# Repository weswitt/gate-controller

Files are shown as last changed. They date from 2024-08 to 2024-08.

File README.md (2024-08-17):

This project is a PCB design for controlling a Liftmaster gate operator from Home Assistant. 

The PCB design was done in KiCad 8.0, which is an open source electronic design tool. This project includes all of the KiCad project files so that you can modify the PCB if needed. I've also included a GERBER.ZIP file that can be used to simply have the PCB printed by someplace like JLPCB.

This project includes a bill of materials with URLs for all the parts necessary to build the board. I've sourced the part from DigiKey and Amazon.

The integration of the gate controller into Home Assistant is accomplished using ESPHome. This project includes the YAML file necessary to build and flash the firmware into the gate controller. You'll need to edit the YAML file and change the lines specified to customize to your environment.

This project includes datasheets for every component used on the gate controller board.

The gate controller board uses an ESP32-WROOM-32U microcontroller. This variant of the ESP32 uses an external antenna to improve the Wifi connectivity.

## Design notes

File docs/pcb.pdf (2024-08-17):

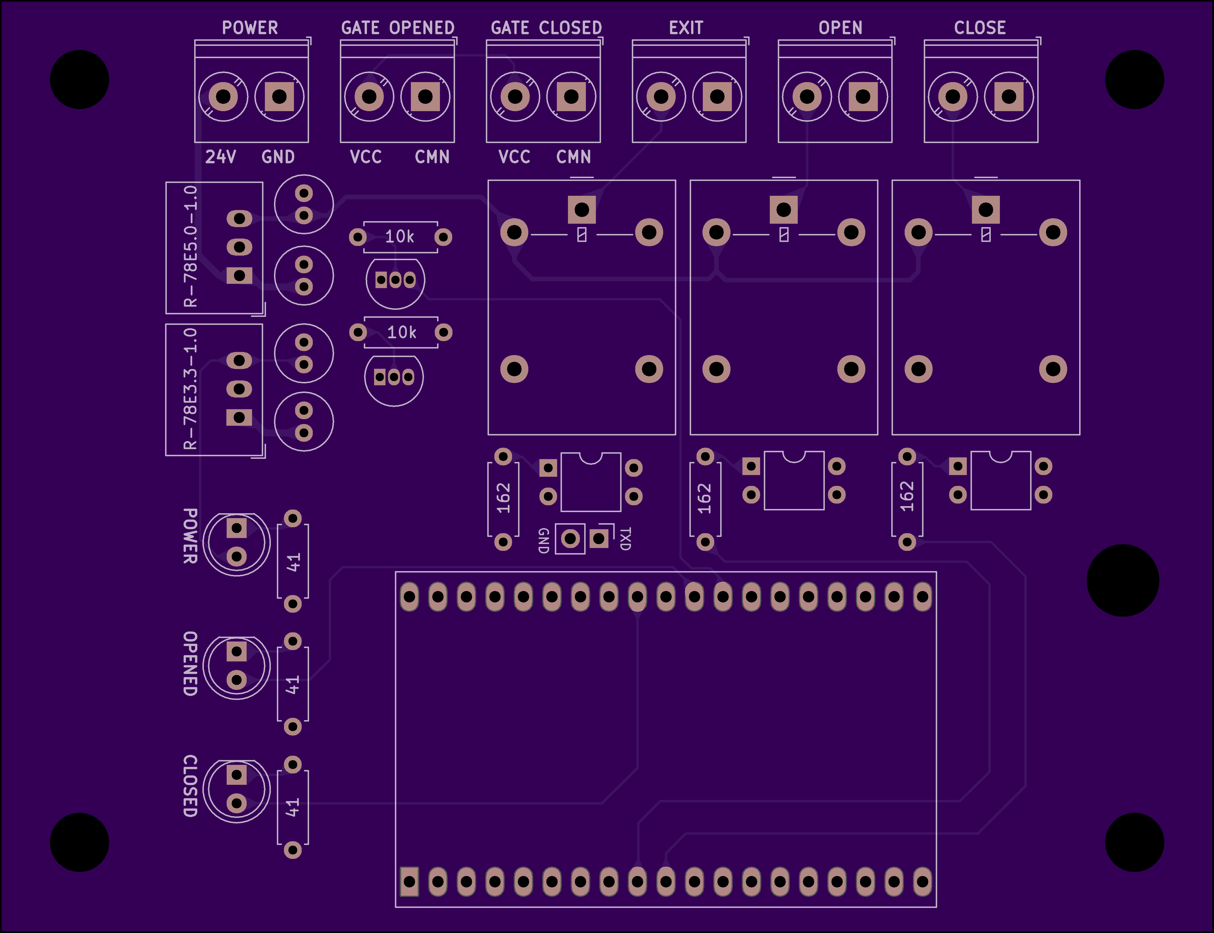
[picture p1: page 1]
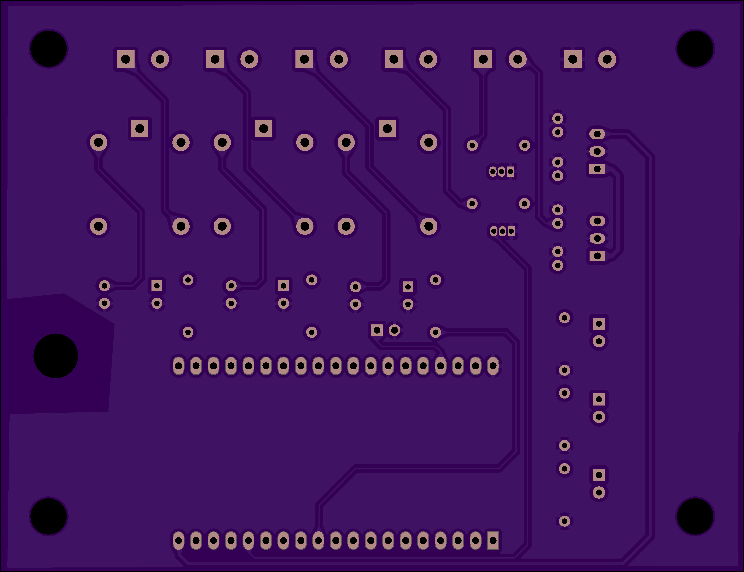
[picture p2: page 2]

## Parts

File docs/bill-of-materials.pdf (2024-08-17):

Item | Qty | Price | Extended | URL
relay | 3 | $1.62 | $4.86 | https://www.digikey.com/en/products/detail/omron-electronics-inc-emc-div/G5LE-1A4-DC5/369019
2n2222 | 2 | $0.40 | $0.80 | https://www.digikey.com/en/products/detail/onsemi/PN2222ABU/6534
fod852 | 3 | $1.08 | $3.24 | https://www.digikey.com/en/products/detail/onsemi/FOD852/1054017
terminal | 6 | $0.50 | $3.00 | https://www.digikey.com/en/products/detail/phoenix-contact/1935161/568614
capacitor | 4 | $0.38 | $1.52 | https://www.digikey.com/en/products/detail/nichicon/UPW1V100MDD/589590
red led | 1 | $0.36 | $0.36 | https://www.digikey.com/en/products/detail/liteon/LTL2R3KEK/573572
green led | 1 | $0.38 | $0.38 | https://www.digikey.com/en/products/detail/liteon/LTL2P3KGKNN/573567
yellow led | 1 | $0.40 | $0.40 | https://www.digikey.com/en/products/detail/liteon/LTL2R3KSK/573576
3v3 converter | 1 | $3.92 | $3.92 | https://www.digikey.com/en/products/detail/recom-power/r-78e3-3-1-0/5327711
5v converter | 1 | $3.92 | $3.92 | https://www.digikey.com/en/products/detail/recom-power/R-78E5-0-1-0/4930585
162 resistor | 3 | $0.10 | $0.30 | https://www.digikey.com/en/products/detail/yageo/MFR-25FBF52-162R/12837
41 resistor | 3 | $0.10 | $0.30 | https://www.digikey.com/en/products/detail/yageo/MFR-25FBF52-41R2/12720
10k resistor | 2 | $0.10 | $0.20 | https://www.digikey.com/en/products/detail/yageo/MFR-25FBF52-10K/13219
esp32u | 1 | $9.99 | $9.99 | https://www.amazon.com/dp/B09BM1QW29
antennea | 1 | $8.59 | $8.59 | https://www.amazon.com/dp/B01KBU61S8

$41.78

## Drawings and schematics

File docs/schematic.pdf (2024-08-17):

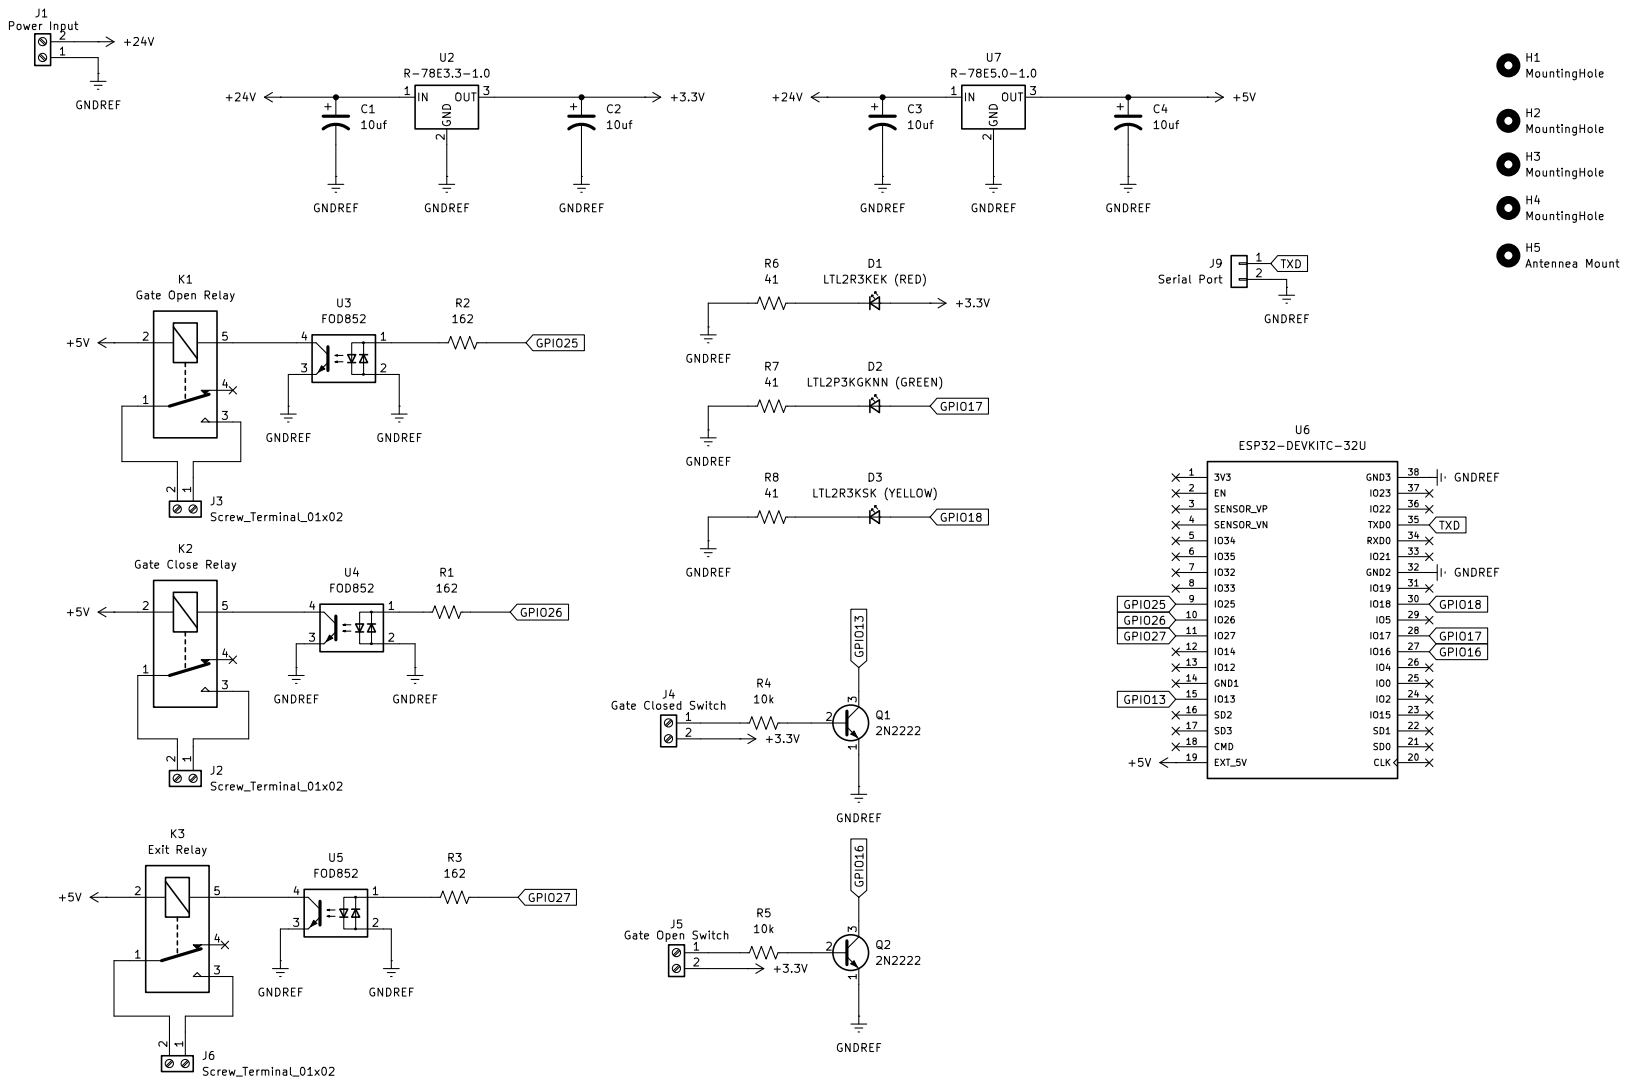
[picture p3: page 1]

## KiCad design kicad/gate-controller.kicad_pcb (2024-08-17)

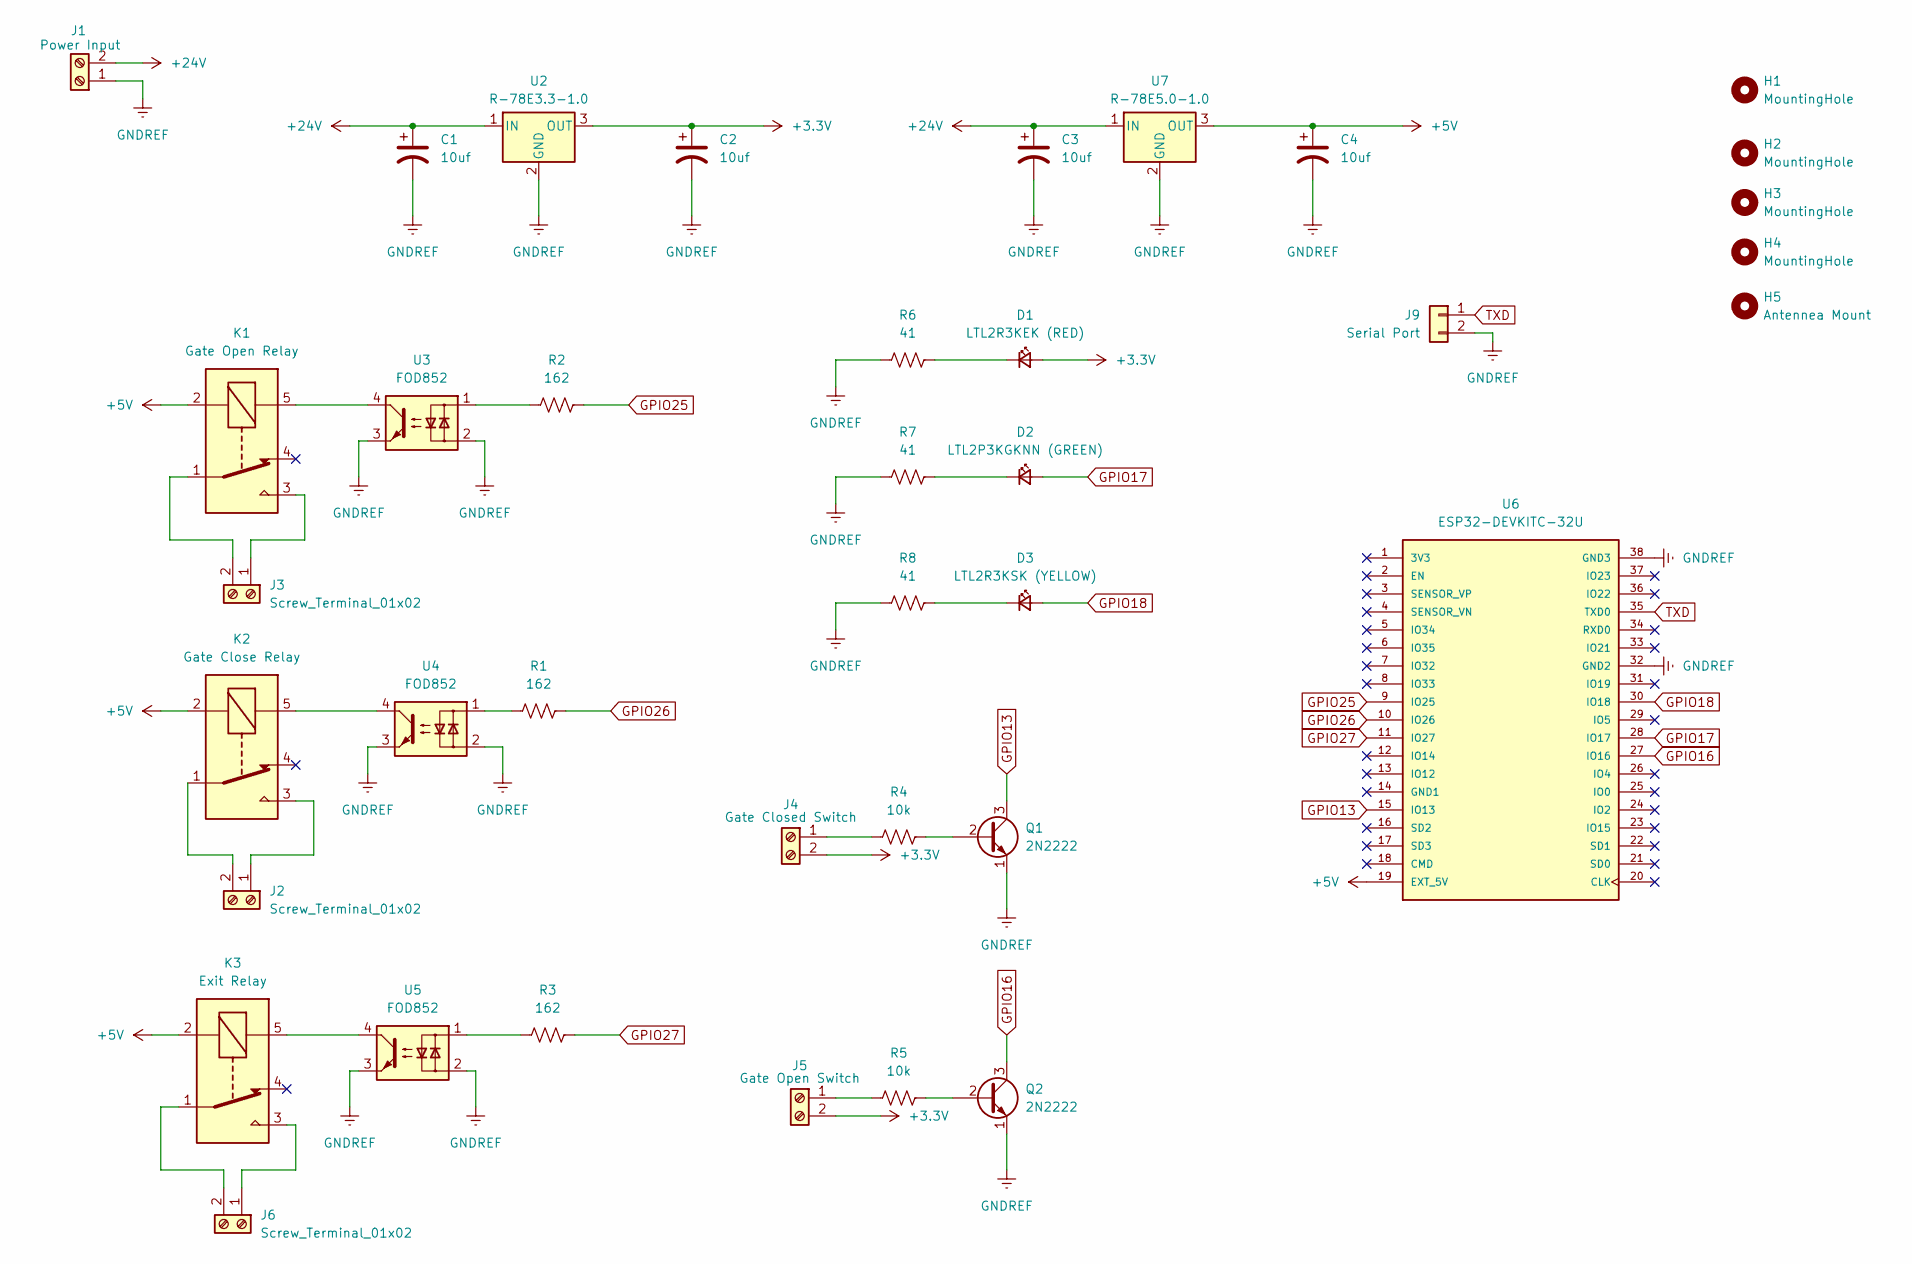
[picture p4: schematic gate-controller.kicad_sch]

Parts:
C1, C2, C3, C4: 10uf; C_Radial_D5.0mm_H11.0mm_P2.00mm
D1: LTL2R3KEK (RED); LED_D5.0mm_Clear
D2: LTL2P3KGKNN (GREEN); LED_D5.0mm_Clear
D3: LTL2R3KSK (YELLOW); LED_D5.0mm_Clear
H1, H2, H3, H4: MountingHole; MountingHole_5.3mm_M5
H5: Antennea Mount; MountingHole_6.5mm
J1: Power Input; TerminalBlock_Phoenix_PT-1,5-2-5.0-H_1x02_P5.00mm_Horizontal
J2, J3, J6: Screw_Terminal_01x02; TerminalBlock_Phoenix_PT-1,5-2-5.0-H_1x02_P5.00mm_Horizontal
J4: Gate Closed Switch; TerminalBlock_Phoenix_PT-1,5-2-5.0-H_1x02_P5.00mm_Horizontal
J5: Gate Open Switch; TerminalBlock_Phoenix_PT-1,5-2-5.0-H_1x02_P5.00mm_Horizontal
J9: Serial Port; PinHeader_1x02_P2.54mm_Vertical
K1: Gate Open Relay; Relay_SPDT_Omron-G5LE-1
K2: Gate Close Relay; Relay_SPDT_Omron-G5LE-1
K3: Exit Relay; Relay_SPDT_Omron-G5LE-1
Q1, Q2: 2N2222; TO-92_Reverse
R1, R2, R3: 162; R_Axial_DIN0207_L6.3mm_D2.5mm_P7.62mm_Horizontal
R4, R5: 10k; R_Axial_DIN0207_L6.3mm_D2.5mm_P7.62mm_Horizontal
R6, R7, R8: 41; R_Axial_DIN0207_L6.3mm_D2.5mm_P7.62mm_Horizontal
U2: R-78E3.3-1.0; Converter_DCDC_RECOM_R-78E-0.5_THT
U3, U4, U5: FOD852; DIP-4_W7.62mm
U6: ESP32-DEVKITC-32U
U7: R-78E5.0-1.0; Converter_DCDC_RECOM_R-78E-0.5_THT

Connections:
+3.3V: C2.1, D1.2 (A), J4.2, J5.2, U2.3 (OUT)
+5V: C4.1, K1.2, K2.2, K3.2, U6.19 (EXT_5V), U7.3 (OUT)
+24V: C1.1, C3.1, J1.2, U2.1 (IN), U7.1 (IN)
GNDREF: C1.2, C2.2, C3.2, C4.2, J1.1, J9.2, Q1.1 (E), Q2.1 (E), R6.1, R7.1, R8.1, U2.2 (GND), U3.2, U3.3, U4.2, U4.3, U5.2, U5.3, U6.32 (GND2), U6.38 (GND3), U7.2 (GND)
GPIO13: Q1.3 (C), U6.15 (IO13)
GPIO16: Q2.3 (C), U6.27 (IO16)
GPIO17: D2.2 (A), U6.28 (IO17)
GPIO18: D3.2 (A), U6.30 (IO18)
GPIO25: R2.2, U6.9 (IO25)
GPIO26: R1.2, U6.10 (IO26)
GPIO27: R3.2, U6.11 (IO27)
unnamed: D1.1 (K), R6.2
unnamed: D2.1 (K), R7.2
unnamed: D3.1 (K), R8.2
unnamed: J2.1, K2.3
unnamed: J2.2, K2.1
unnamed: J3.1, K1.3
unnamed: J3.2, K1.1
unnamed: J4.1, R4.1
unnamed: J5.1, R5.1
unnamed: J6.1, K3.3
unnamed: J6.2, K3.1
unnamed: K1.5, U3.4
unnamed: K2.5, U4.4
unnamed: K3.5, U5.4
unnamed: Q1.2 (B), R4.2
unnamed: Q2.2 (B), R5.2
unnamed: R1.1, U4.1
unnamed: R2.1, U3.1
unnamed: R3.1, U5.1
TXD: J9.1, U6.35 (TXD0)

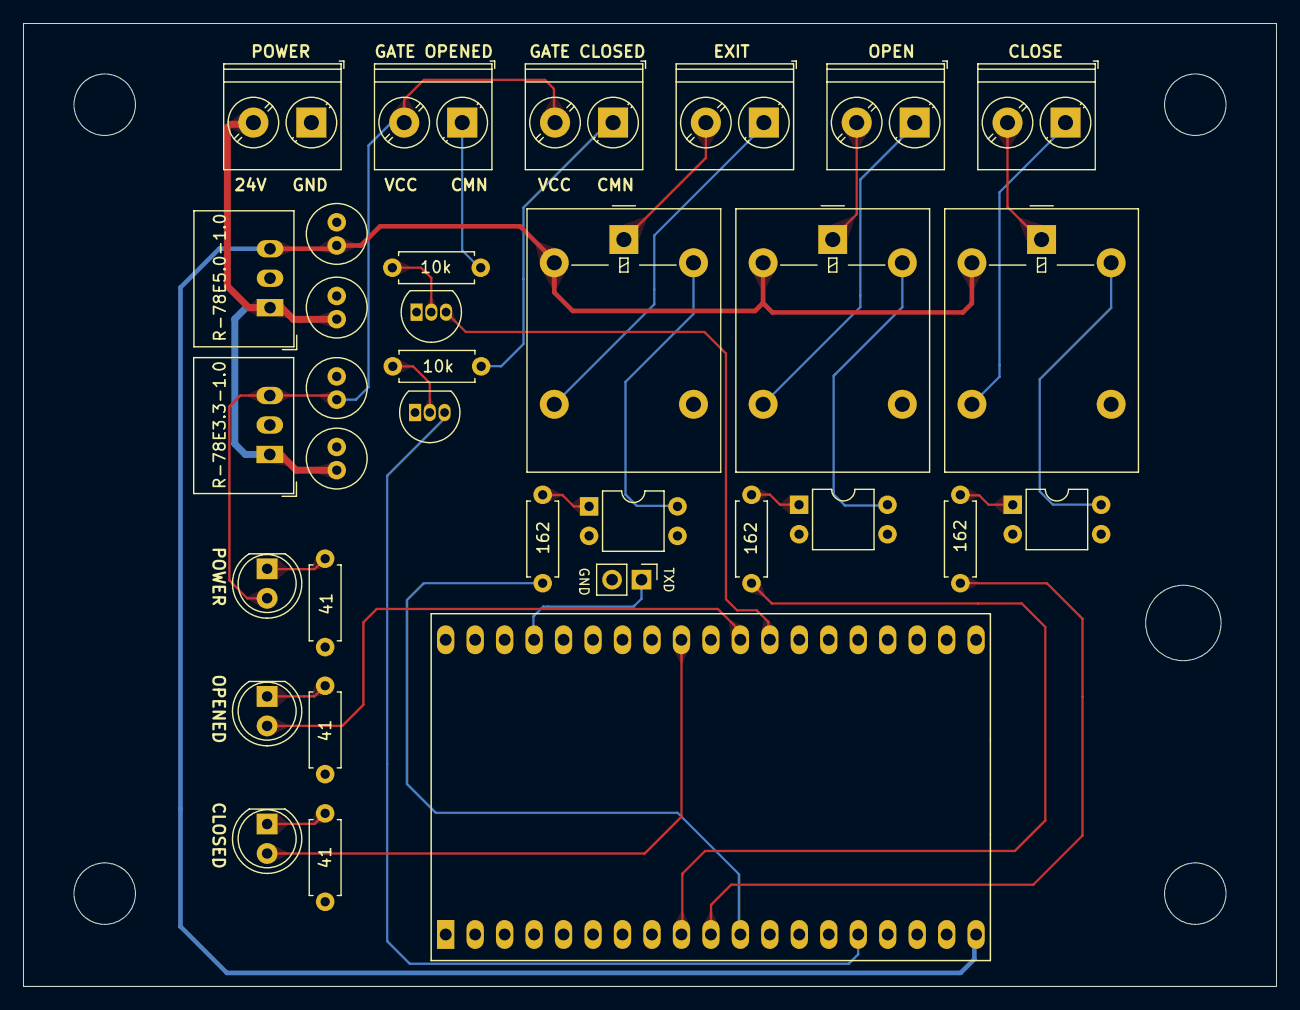
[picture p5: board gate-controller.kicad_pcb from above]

Board: 2 copper layers, 108.0 x 83.0 mm, 38 parts (0 on the bottom side), 31 nets.

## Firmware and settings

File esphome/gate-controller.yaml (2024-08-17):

esp32:
  board: esp32doit-devkit-v1

esphome:
  name: **your-name**
  friendly_name: **your-friendly-name**

api:

logger:
  baud_rate: 0
#  baud_rate: 115200
#  level: VERBOSE

ota:

web_server:
  port: 80

wifi:
  ssid: **your-ssid**
  password: **your-password**
  manual_ip:
    static_ip: **your-ip**
    gateway: **your-gateway**
    subnet: **your-subnet**

button:
  - platform: restart
    name: Restart

text_sensor:
  - platform: wifi_info
    ip_address:
      name: "IP Address"
      id: ip_address
      icon: mdi:ip-network
    ssid:
      name: SSID
      id: ssid
      icon: mdi:wifi

sensor:
  - platform: uptime
    name: Uptime
  - platform: wifi_signal
    name: "WiFi Signal"
    id: wifi_signal_strength
    update_interval: 60s
    icon: mdi:wifi-strength-1

light:
  - platform: status_led
    id: opened_led
    pin: GPIO17
    restore_mode: ALWAYS_OFF
  - platform: status_led
    id: closed_led
    pin: GPIO18
    restore_mode: ALWAYS_OFF

binary_sensor:
  - platform: gpio
    filters:
      - invert:
    pin:
      number: GPIO13
      mode:
        input: true
        pullup: true
    name: "Closed Sensor"
    id: closed_sensor
    icon: mdi:gate
    on_press:
      then:
        - light.turn_on: closed_led
        - light.turn_off: opened_led
  - platform: gpio
    filters:
      - invert:
    pin:
      number: GPIO16
      mode:
        input: true
        pullup: true
    name: "Open Sensor"
    id: open_sensor
    icon: mdi:gate-open
    on_press:
      then:
        - light.turn_on: opened_led
        - light.turn_off: closed_led

switch:
  - platform: gpio
    pin: GPIO25
    name: "Open Switch"
    id: open_switch
    icon: mdi:gate
    on_turn_on:
      - delay: 200ms
      - switch.turn_off: open_switch
  - platform: gpio
    pin: GPIO26
    name: "Close Switch"
    id: close_switch
    icon: mdi:gate
    on_turn_on:
      - delay: 200ms
      - switch.turn_off: close_switch
  - platform: gpio
    pin: GPIO27
    name: "Exit Switch"
    id: exit_switch
    icon: mdi:gate
    on_turn_on:
      - delay: 200ms
      - switch.turn_off: exit_switch
